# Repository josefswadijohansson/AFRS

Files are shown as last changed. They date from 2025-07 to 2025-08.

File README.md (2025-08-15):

# AFRS

[][cc-by-nc-sa]

Just a fun side electronic project, an Automatic Fishing Reel Spooler(not for when you are on the lake, but before when you are putting line on the fishing reel).

## Demostration

[Showcasing Video](https://www.youtube.com/shorts/x-qOwM7sNGY)

## Software Used

- [FreeCAD 1.0](https://www.freecad.org/)
- [OrcaSlicer](https://orcaslicer.com/)
- [Blender](https://www.blender.org/)

## Library Used
- LittleFS
- AccelStepper
- ArduinoJson
- Wifi
- Webserver

## Concept Picture
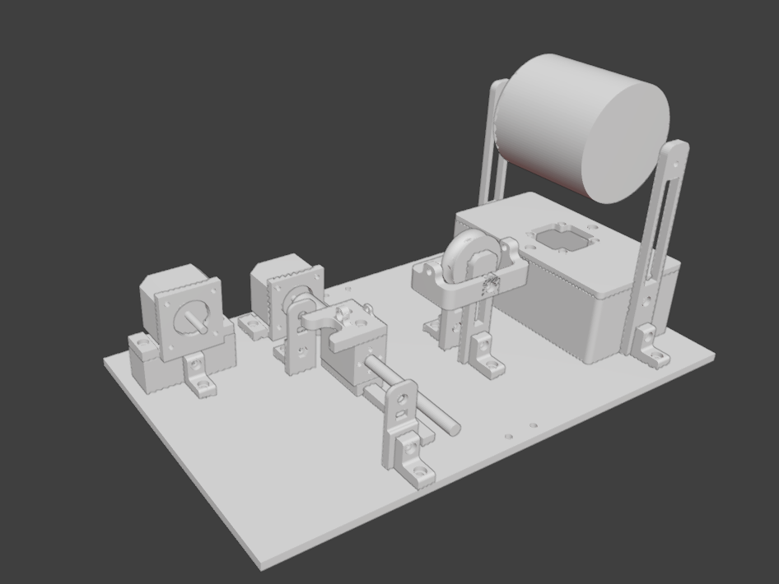
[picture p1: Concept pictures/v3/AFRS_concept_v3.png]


## End Result
<p float="left">
  
  
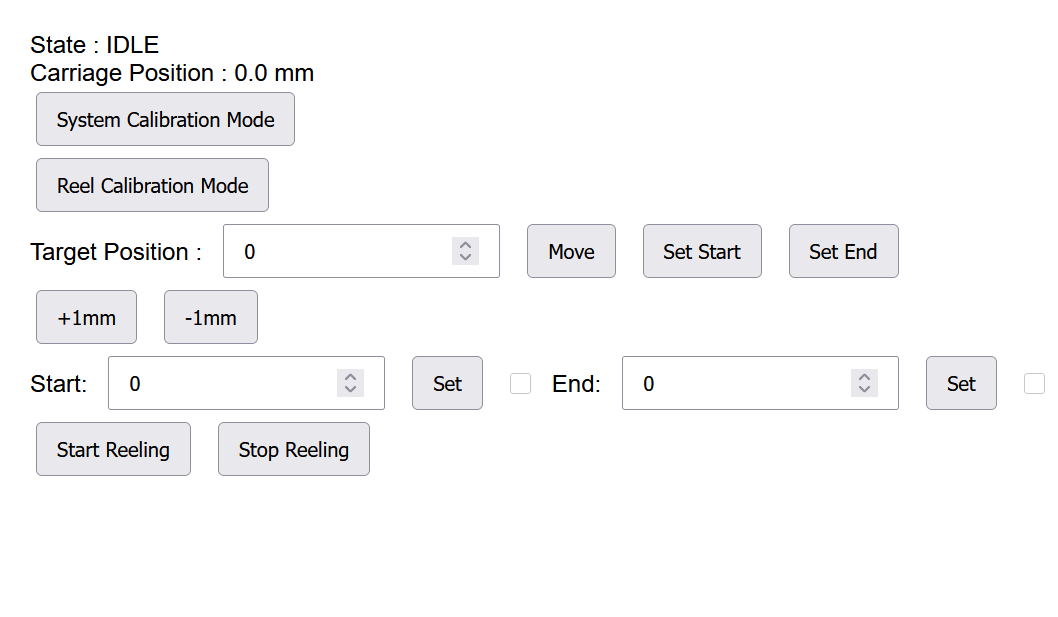
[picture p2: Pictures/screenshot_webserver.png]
  
</p>

## Components used

- 2x ESP32-C3 Mini development boards
- 2x Small "Pancake" variants of Nema 17
- 2x TMC2208 Driver module
- 150mm T8 Leadscrew
- 100mm Linear rail
- 3.3v Small laser guide
- 2x Push buttons acting as limit switches

## Improvements and fixes

- For the fishing line distance measuring, i was planning on having a measuring wheel with magnets glued to them, and when fishing line was reeled on to the new fishing reel it would spin and activate a hall sensor and for each pulse a distance would be added to the counting, issue is when i had printed the measuring wheel and then glued magnets, i realised that the hall sensor only activated on one polarity, which i didn't know. To not have this issue blocking the development of the webserver i instead removed and put that part of the project in pause for later testing and adding in later. So in the future i want the user to be able to set a X amount of meters of line to be only feed to the reel via the webserver interface.
- For now it uses TCP communication, issue is that since status update is wanted on the webserver to know the device position and state, TCP is a bit blocking on the ESP32, meaning i would prefer to maybe use UDP or some other communcation type to not block the device but to know the status of the device in the future.
- Could make the webserver interface better looking and user friendly, for now it's in the most basic form, issue i wanted to reduce file size since i had limited 400kb memory on the ESP32-C3
- Instead of hosting a webserver i could develop a desktop .NET program that talks to the ESP32-C3 devices

## License

This work is licensed under a
[Creative Commons Attribution-NonCommercial-ShareAlike 4.0 International License][cc-by-nc-sa].

[][cc-by-nc-sa]

[cc-by-nc-sa]: http://creativecommons.org/licenses/by-nc-sa/4.0/
[cc-by-nc-sa-image]: https://licensebuttons.net/l/by-nc-sa/4.0/88x31.png
[cc-by-nc-sa-shield]: https://img.shields.io/badge/License-CC%20BY--NC--SA%204.0-lightgrey.svg

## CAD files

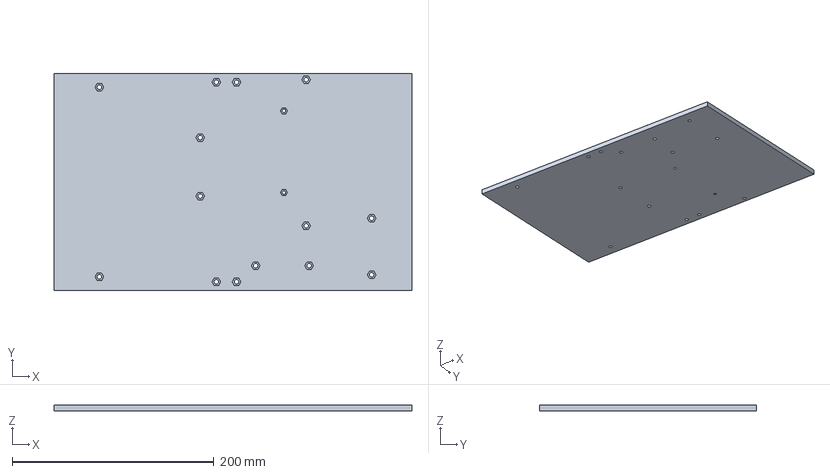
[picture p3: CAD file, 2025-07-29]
CAD/V3/BasePlate/BasePlate.FCStd
355.0 x 215.0 x 6.00 mm

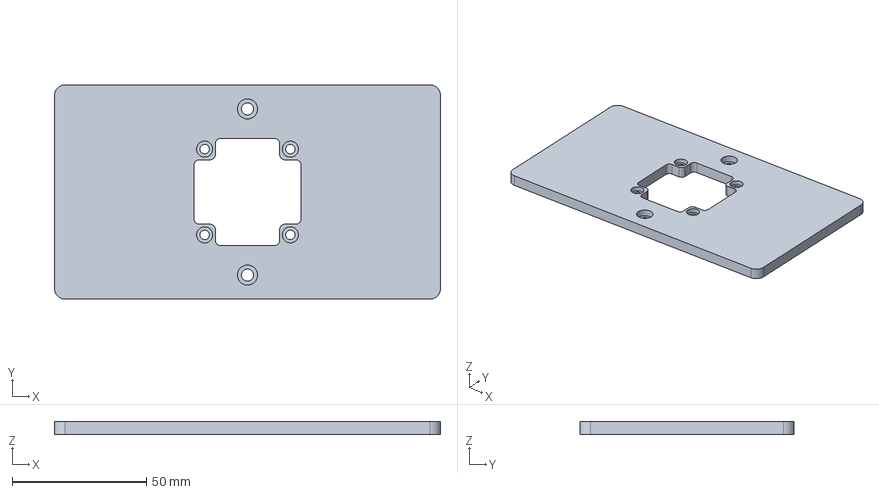
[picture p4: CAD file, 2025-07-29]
CAD/V3/ElectronicHub/ElectronicHub-Lid.FCStd
144.0 x 80.0 x 5.00 mm

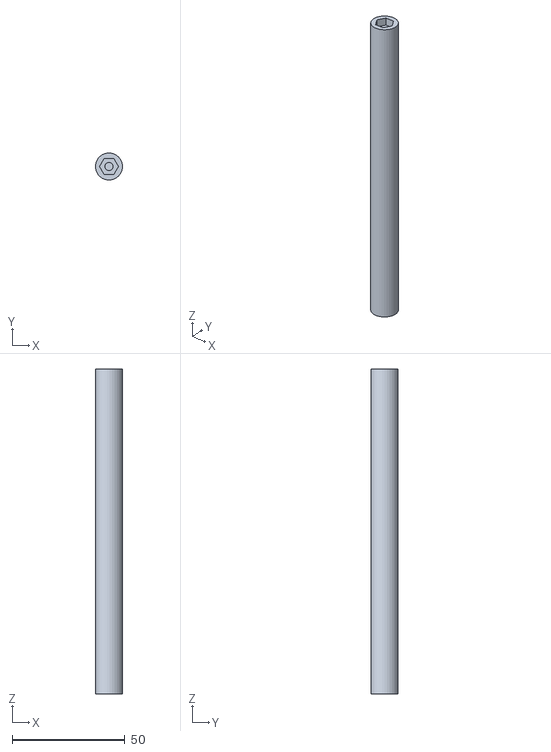
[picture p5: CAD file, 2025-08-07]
CAD/V3/FishingLineAxle/FishingLineAxle-Body.stl
12.0 x 12.0 x 144.0

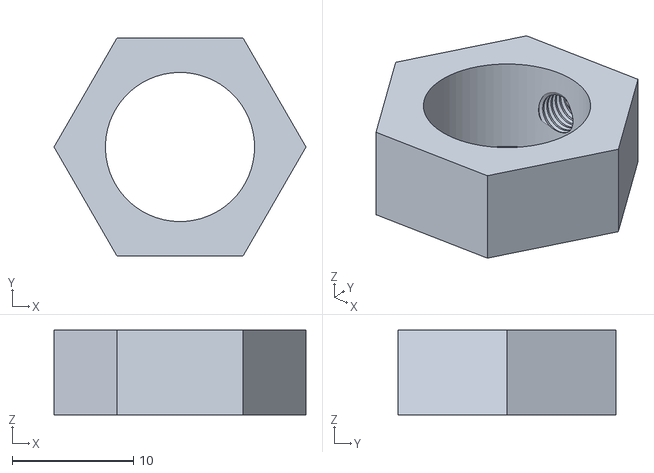
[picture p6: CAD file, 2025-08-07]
CAD/V3/FishingLineAxleTensioningNut/FishingLineAxleTensioningNut-Body.stl
20.8 x 18.0 x 7.00

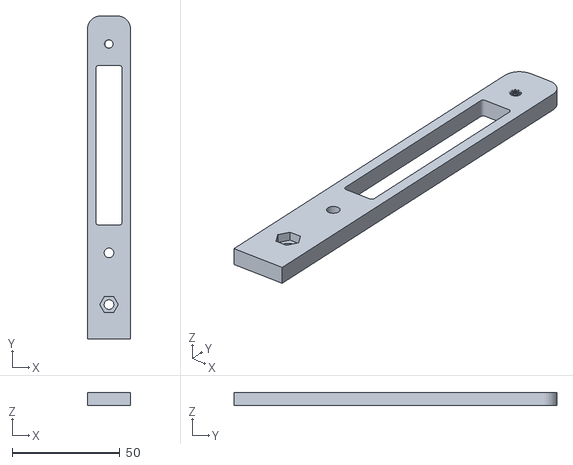
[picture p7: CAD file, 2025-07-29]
CAD/V3/FishingLineSpoolArm/FishingLineSpoolArm-Body.stl
20.0 x 150.0 x 6.00

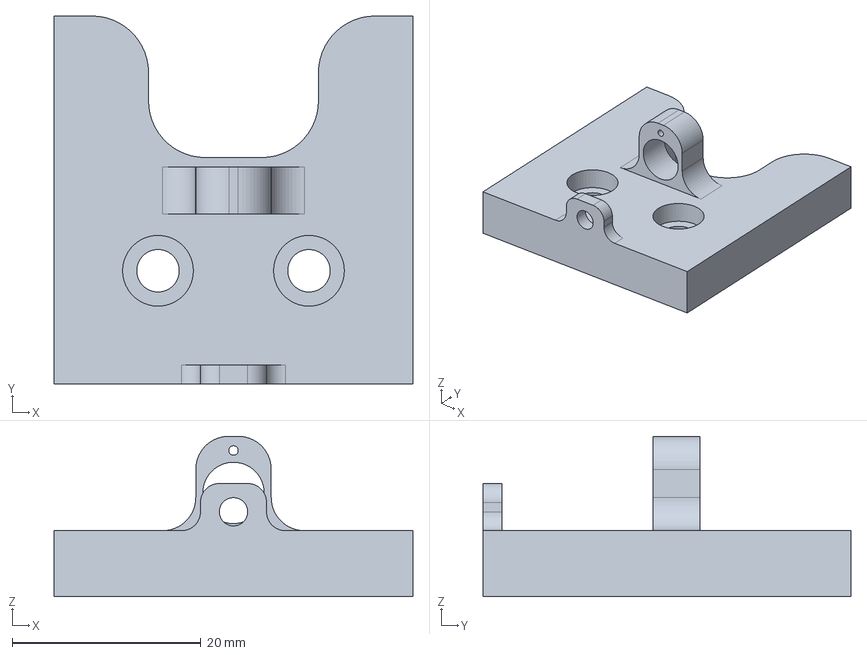
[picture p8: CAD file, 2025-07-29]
CAD/V3/Guide/Guide.FCStd
38.0 x 39.0 x 17.0 mm

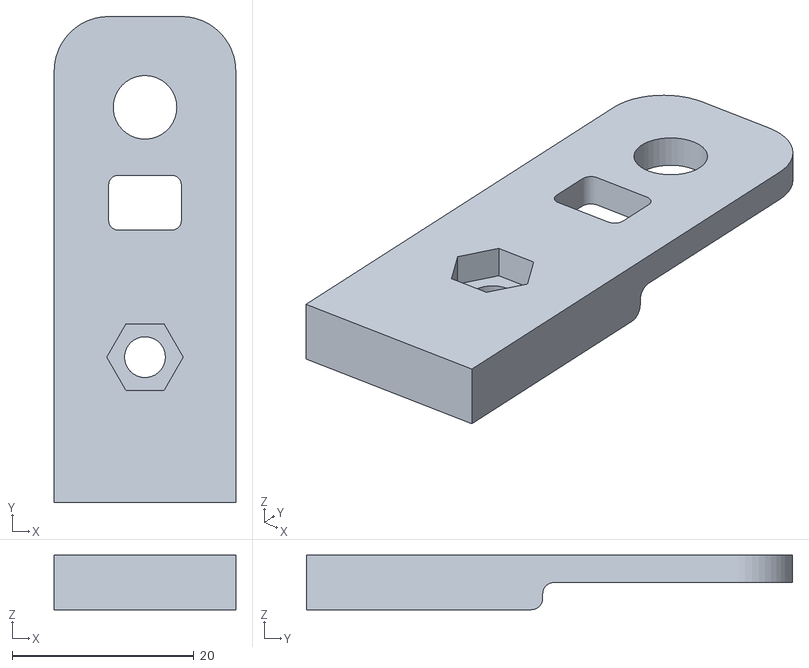
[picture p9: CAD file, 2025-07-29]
CAD/V3/LimitSwitchArm/LimitSwitchArm-Body.stl
20.0 x 53.5 x 6.00

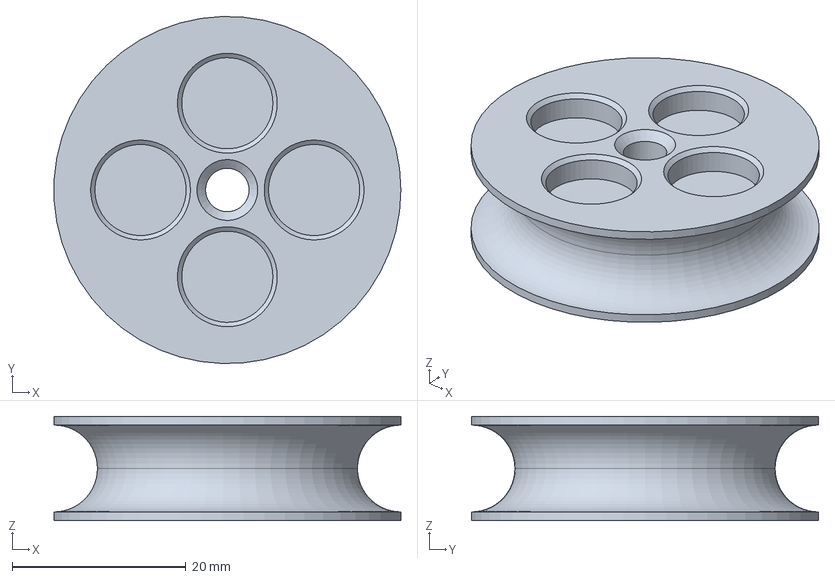
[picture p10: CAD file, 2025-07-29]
CAD/V3/MeasuringWheel/MeasuringWheel.FCStd
40.0 x 40.0 x 12.0 mm

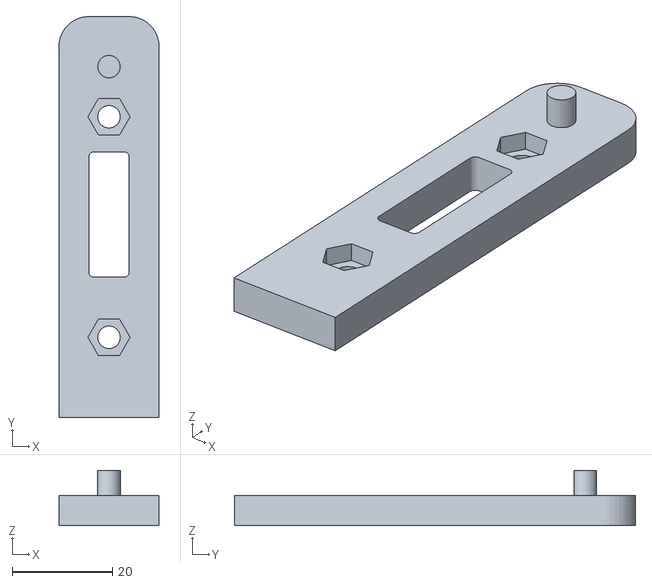
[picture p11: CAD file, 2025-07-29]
CAD/V3/MeasuringWheelArm/MeasuringWheelArm-Body.stl
20.0 x 80.0 x 11.0

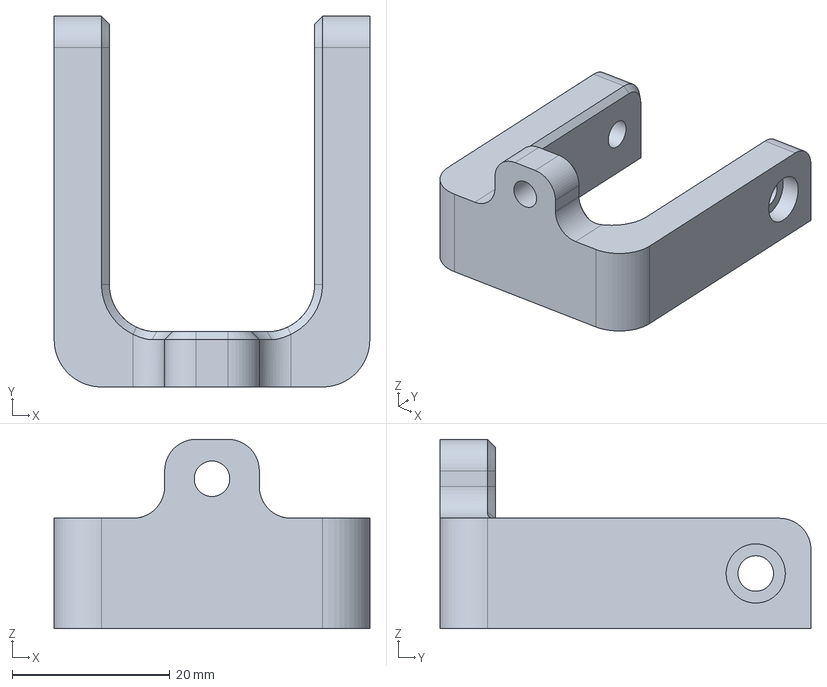
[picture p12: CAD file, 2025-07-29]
CAD/V3/MeasuringWheelArmAttachment-Guide/MeasuringWheelArmAttachment-Guide.FCStd
40.0 x 47.0 x 24.0 mm

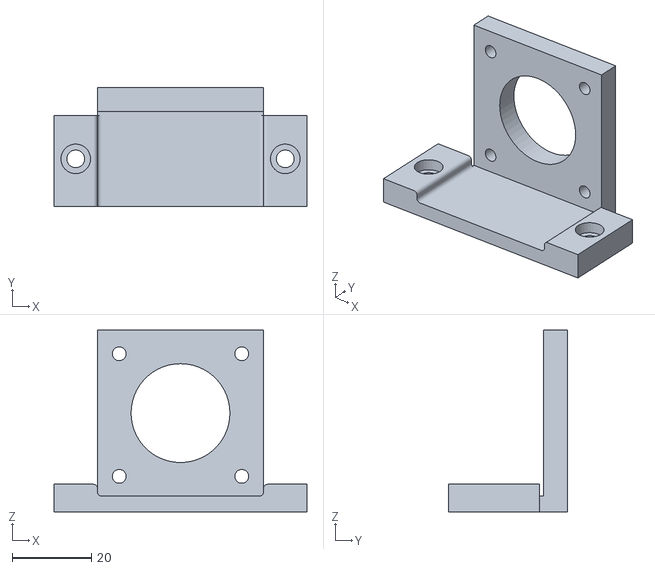
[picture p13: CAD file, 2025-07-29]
CAD/V3/Nema17Bracket/Nema17-Bracket-Body-v2.stl
64.0 x 30.0 x 46.0

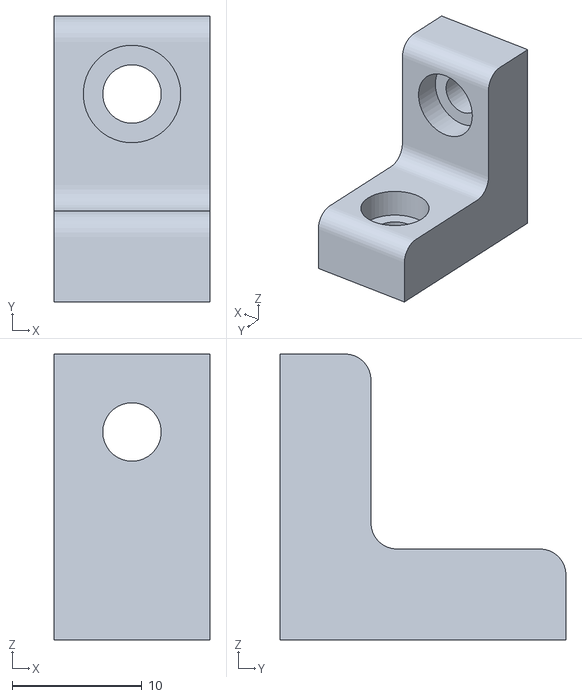
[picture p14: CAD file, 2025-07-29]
CAD/V3/PartLinker/PartLinker-Body.stl
12.0 x 22.0 x 22.0

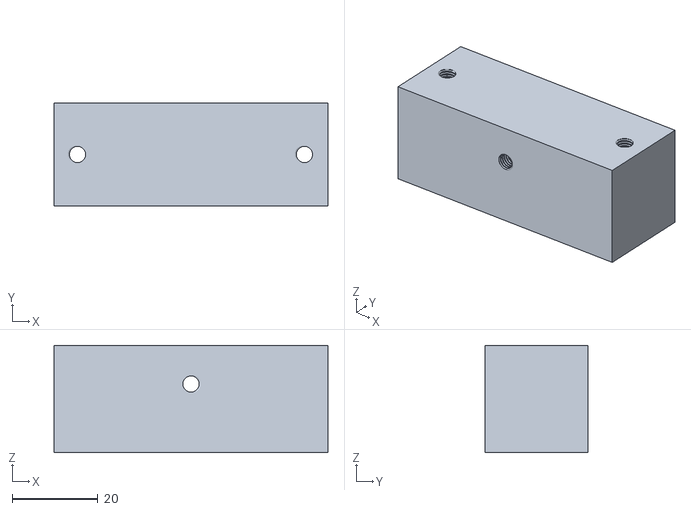
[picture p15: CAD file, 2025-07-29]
CAD/V3/ReelMotorMountAdapterBlock/ReelMotorMountAdapterBlock-Body.stl
64.0 x 24.0 x 25.0

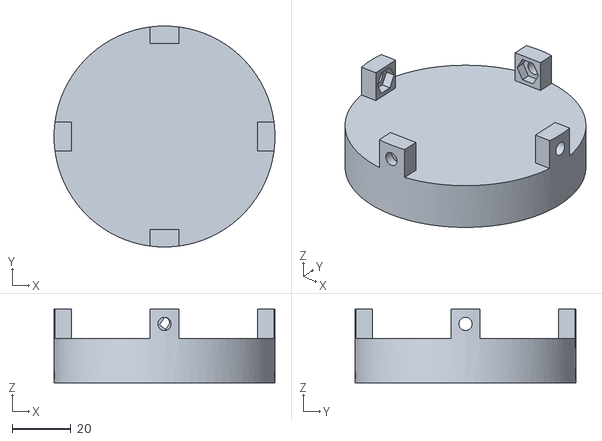
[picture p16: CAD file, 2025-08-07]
CAD/V3/ReelMount/ReelMount-Body-v3.stl
75.0 x 75.0 x 25.0

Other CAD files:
CAD/V3/BasePlate/BasePlate-Body-1.stl
CAD/V3/ElectronicHub/ElectronicHub-Body.stl
CAD/V3/FishingLineAxle/FishingLineAxle-Body-correction.stl
CAD/V3/FishingLineAxleTensioningNut/FishingLineAxleTensioningNut.FCStd
CAD/OLD_CAD_FILES/BasePlate/BasePlateAFRS-Link-Body.stl
CAD/OLD_CAD_FILES/BasePlate/BasePlateAFRS-Link.FCStd
CAD/OLD_CAD_FILES/BasePlate/BasePlateAFRS-Part1.stl
CAD/OLD_CAD_FILES/BasePlate/BasePlateAFRS-Part2.stl
CAD/OLD_CAD_FILES/BasePlate/BasePlateAFRS-v2-Body.stl
CAD/OLD_CAD_FILES/BasePlate/BasePlateAFRS-v2.FCStd
CAD/OLD_CAD_FILES/BasePlate/BasePlateAFRS.FCStd
CAD/OLD_CAD_FILES/BasePlate/BasePlateAFRS.stl
CAD/OLD_CAD_FILES/Crank-and-Slide/Carriage/Carriage-Body-v2.stl
CAD/OLD_CAD_FILES/Crank-and-Slide/Carriage/Carriage-Body.stl
CAD/OLD_CAD_FILES/Crank-and-Slide/Carriage/Carriage.FCStd
CAD/OLD_CAD_FILES/Crank-and-Slide/CarriageLineGuide/CarriageLineGuide-Body.stl
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

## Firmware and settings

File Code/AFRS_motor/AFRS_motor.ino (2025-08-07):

#include <AccelStepper.h>
#include <ArduinoJson.h>
#include <WiFi.h>

// === Pin Definitions ===
#define M1_STEP_PIN 0    // Reel motor step
#define M1_DIR_PIN  1    // Reel motor direction

#define M2_STEP_PIN 2    // Carriage motor step
#define M2_DIR_PIN  3    // Carriage motor direction

#define START_SW_PIN 6    // Home limit switch
#define END_SW_PIN  5    // End limit switch

// Wi-Fi credentials
const char* ssid = "";
const char* password = "";

WiFiServer motorServer(3333);  // Open port 3333
WiFiClient activeClient;       // Store the current client

String recvBuffer = "";

AccelStepper reelMotor(AccelStepper::DRIVER, M1_STEP_PIN, M1_DIR_PIN);
AccelStepper carriageMotor(AccelStepper::DRIVER, M2_STEP_PIN, M2_DIR_PIN);

// === Motor Configuration ===
const int MOTOR_STEPS = 200;                    // 200 steps/rev for NEMA 17
const int MICROSTEPPING = 8;                    // Set on driver board (MS1/MS2 jumpers)
const float DISTANCE_PER_REVOLUTION = 2.0;      // mm per revolution (best to do a revolution by hand and measure distance and input it here)
const float STEPS_PER_MM = (MOTOR_STEPS * MICROSTEPPING) / DISTANCE_PER_REVOLUTION;

// === Speed Settings ===
const float REEL_RPM = 40;    // Reel motor speed
float CARRIAGE_RPM = 100;     // Carriage motor speed (will be dynamically set)
#define FORWARD -1            // In my setup the carriage is moving forward is in negative speed, meaning away from the motor, that why we need to invert the movement in tracking

// System state management
enum SystemState {
  IDLE,
  SYSTEM_CALIBRATION,
  REEL_CALIBRATION,
  REELING
};
SystemState currentSystemState = IDLE;

enum SystemCalibrationState {
  FIND_START,
  FIND_END
};
SystemCalibrationState systemCalibrationState = FIND_START;

// Position tracking
float railLength = 0;
float currentPositionMM = 0;
float targetPosition = 0;
bool isMovingToEnd = false;

// Gap values
float reelGapStartPosition = -1;
float reelGapEndPosition = -1;

bool starterSet = false;  // Is start gap position set?
bool endSet = false;      // Is start gap position set?

void setup() {
  Serial.begin(115200);

  Serial.println("Motor ESP Connecting");
  // Connect to Wi-Fi
  WiFi.begin(ssid, password);
  while (WiFi.status() != WL_CONNECTED) {
    delay(500);
    Serial.print(".");
  }
  Serial.println("\nMotor ESP connected. IP: " + WiFi.localIP().toString());

  // FIXME : Perhaps use UDP communication instead maybe it will not block the ESP32C3 as much
  motorServer.begin();  // Start TCP server

  pinMode(START_SW_PIN, INPUT_PULLUP);
  pinMode(END_SW_PIN, INPUT_PULLUP);

  // Configure reel motor
  reelMotor.setMaxSpeed((REEL_RPM * MOTOR_STEPS * MICROSTEPPING) / 60.0);
  reelMotor.setSpeed(-reelMotor.maxSpeed());  // To reel the line in toward the fishing reel, i need the fishing reel to move anti-clockwise
  reelMotor.setMinPulseWidth(50);

  // Configure carriage motor
  carriageMotor.setMaxSpeed((CARRIAGE_RPM * MOTOR_STEPS * MICROSTEPPING) / 60.0);
  carriageMotor.setSpeed(carriageMotor.maxSpeed());
  carriageMotor.setMinPulseWidth(50);
}

void loop() {
  // Accept new clients
  if (!activeClient || !activeClient.connected()) {
    activeClient = motorServer.available();
  }

  if (activeClient && activeClient.connected() && activeClient.available()) {
    while (activeClient.available()) {
      char c = activeClient.read();

      if (c == '\n') {
        recvBuffer.trim();  // Remove trailing \r or whitespace
        if (recvBuffer.length() > 0) {
          handleCommand(recvBuffer, activeClient);
        }
        recvBuffer = "";  // Reset for next command
      } else {
        recvBuffer += c;
        // Optional: protect against overflow
        if (recvBuffer.length() > 200) recvBuffer = "";  // Reset if too long
      }
    }
  }

  // Main state machine
  switch (currentSystemState) {
    case IDLE: break;
    case REELING: runReeling(); break;
    case REEL_CALIBRATION: runCalibration(); break;
    case SYSTEM_CALIBRATION:
      if (systemCalibrationState == FIND_START) runFindStart();
      else if (systemCalibrationState == FIND_END) runFindEnd();
      break;
  }
}

void runFindStart() {
  // Force the carriage motor to find the start switch by moving it positive direction, meaning toward the motor
  if(carriageMotor.speed() <= 0){ 
    carriageMotor.setSpeed(carriageMotor.maxSpeed());
  }

  carriageMotor.runSpeed();

  // 
  if (digitalRead(START_SW_PIN) == LOW) {
    carriageMotor.stop();
    carriageMotor.setSpeed(0);
    currentPositionMM = 0;  // Start from zero
    carriageMotor.setCurrentPosition(0);
    carriageMotor.setSpeed(carriageMotor.maxSpeed());  // Always move forward from here
    systemCalibrationState = FIND_END;
  }
}

void runFindEnd() {

  // Force the carriage motor to find the end switch by moving it negative direction, meaning away from the motor
  if(carriageMotor.speed() >= 0){
    carriageMotor.setSpeed(carriageMotor.maxSpeed() * FORWARD);
  }

  if (carriageMotor.runSpeed()) {
    currentPositionMM += (1.0 / STEPS_PER_MM); // Calculate the new position when the motor actually does steps
  }

  if (digitalRead(END_SW_PIN) == LOW) {
    carriageMotor.stop();
    carriageMotor.setSpeed(0);

    railLength = currentPositionMM; // Assign the maximum length the motor can travel
    targetPosition = railLength;

    currentSystemState = IDLE;
  }
}

void runReeling() {
  
  if(reelGapStartPosition < 0 || reelGapEndPosition < 0){
    // TODO : Maybe throw an error for the user
    stopMotors();
    return;
  }

  if (isWithinRange(currentPositionMM, reelGapStartPosition, reelGapEndPosition)) {

    if(reelMotor.speed() == 0){
      reelMotor.setSpeed(-reelMotor.maxSpeed());
    }
    reelMotor.runSpeed();
  }

  // === Oscillate effect === 
  if (!isMovingToEnd) {
    if (runMoveToPosition(reelGapStartPosition)) {
      isMovingToEnd = true;
    }
  } else {
    if (runMoveToPosition(reelGapEndPosition)) {
      isMovingToEnd = false;
    }
  }
}

void runCalibration() {
  runMoveToPosition(targetPosition);
}

bool runMoveToPosition(float position) {

  // If it want's to move out of bounds, stop the motors, maybe it will damage the setup
  if(position < 0.0f || position > railLength){
    stopMotors();
    return false;
  }

  float distance = abs(currentPositionMM - position);
  float margin = 0.01f;

  if (distance <= margin) {
    carriageMotor.setSpeed(0);
    carriageMotor.stop();
    return true;
  }

  int direction = sign(position - currentPositionMM);
  int previousDirection = (carriageMotor.speed() / FORWARD) / carriageMotor.maxSpeed();

  if (previousDirection != direction) {
    carriageMotor.setSpeed(carriageMotor.maxSpeed() * direction * FORWARD);
  }

  if (carriageMotor.runSpeed()) {
    currentPositionMM += (carriageMotor.speed() > 0) ? (-1.0 / STEPS_PER_MM) : (1.0 / STEPS_PER_MM);

    if (distance <= margin) {
      carriageMotor.setSpeed(0);
      carriageMotor.stop();
      return true;
    }
  }

  return false;
}

void stopMotors(){
    currentSystemState = IDLE;
    carriageMotor.stop();
    carriageMotor.setSpeed(0);
    reelMotor.stop();
    reelMotor.setSpeed(0);
}

float calculateCarriageRPM(float reelRPM, float gapLengthMM) {
  float timeForReelRevs = 4.0f * 60.0f / reelRPM;
  float mmPerSec = gapLengthMM / timeForReelRevs;
  float carriageRevsPerSec = mmPerSec / DISTANCE_PER_REVOLUTION;
  return carriageRevsPerSec * 60.0f;
}

bool isWithinRange(float currentPosition, float start, float end) {
  return currentPosition >= start && currentPosition <= end;
}

float sign(float value) {
  return float((value > 0) - (value < 0));
}

String stateToString(SystemState systemState) {
  switch(systemState) {
    case IDLE: return "IDLE";
    case REELING: return "REELING";
    case REEL_CALIBRATION: return "REEL_CALIBRATION";
    case SYSTEM_CALIBRATION: return "SYSTEM_CALIBRATION";
    default: return "UNKNOWN";
  }
}

void handleCommand(const String& cmd, WiFiClient& client) {
  if (cmd.startsWith("starter-position-input")) {
    float value;
    int scanned = sscanf(cmd.c_str(), "starter-position-input %f", &value);
    if (scanned == 1) {
      reelGapStartPosition = value;
      starterSet = true;

      if (starterSet && endSet) {
        float gap = reelGapEndPosition - reelGapStartPosition;
        float newCarriageRPM = calculateCarriageRPM(REEL_RPM, gap);
        CARRIAGE_RPM = newCarriageRPM;
        float maxSpeed = (newCarriageRPM * MOTOR_STEPS * MICROSTEPPING) / 60.0;
        carriageMotor.setMaxSpeed(maxSpeed);
      }

      client.println("OK");
    } else {
      client.println("Invalid starter-position-input command");
    }

  } else if (cmd.startsWith("end-position-input")) {
    float value;
    int scanned = sscanf(cmd.c_str(), "end-position-input %f", &value);
    if (scanned == 1) {
      reelGapEndPosition = value;
      endSet = true;

      if (starterSet && endSet) {
        float gap = reelGapEndPosition - reelGapStartPosition;
        float newCarriageRPM = calculateCarriageRPM(REEL_RPM, gap);
        CARRIAGE_RPM = newCarriageRPM;
        float maxSpeed = (newCarriageRPM * MOTOR_STEPS * MICROSTEPPING) / 60.0;
        carriageMotor.setMaxSpeed(maxSpeed);
      }

      client.println("OK");
    } else {
      client.println("Invalid end-position-input command");
    }
  } else if (cmd == "status") {
    StaticJsonDocument<200> doc;
    doc["position"] = currentPositionMM;
    doc["state"] = stateToString(currentSystemState);
    doc["railLength"] = railLength;
    doc["starterSet"] = starterSet;
    doc["endSet"] = endSet;
    String json;
    serializeJson(doc, json);
    client.println(json);

  } else if (cmd == "calibrate") {
    currentSystemState = SYSTEM_CALIBRATION;
    systemCalibrationState = FIND_START;
    client.println("System calibration started");

  } else if (cmd == "reel_cal") {
    if(currentSystemState != REEL_CALIBRATION){
      currentSystemState = REEL_CALIBRATION;
      
    } else {
      currentSystemState = IDLE;
    }

    if(starterSet && endSet){
      targetPosition = (reelGapEndPosition - reelGapStartPosition) / 2.0f;
    }else {
      targetPosition = 0;
    }

    client.println("Reel calibration mode");

  } else if (cmd == "start") {
    if (starterSet && endSet) {
      currentSystemState = REELING;
      client.println("Started reeling");
    } else {
      client.println("Error: Gap not set");
    }

  } else if (cmd == "stop") {
    stopMotors();
    client.println("Stopped");
  } else if (cmd.startsWith("move")) {
    float value;
    int scanned = sscanf(cmd.c_str(), "move %f", &value);
    if (scanned == 1) {
      targetPosition = value;
      currentSystemState = REEL_CALIBRATION;  // Use existing logic to move to target
      client.println("OK");
    } else {
      client.println("Invalid end-position-input command");
    }

  }else {
    client.println("Unknown command");
  }
}

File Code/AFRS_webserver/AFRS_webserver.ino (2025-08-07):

#include <WiFi.h>
#include <WebServer.h>
#include <ArduinoJson.h>
#include <LittleFS.h>

// Wi-Fi credentials
const char* ssid = "";
const char* password = "";

// Web server on port 80
WebServer server(80);

// TCP client for talking to motor ESP
WiFiClient motorClient;
IPAddress motorIP(192, 168, 1, 18); // Motor ESP IP (must be static or fixed by DHCP)

bool starterSet = false;
bool endSet = false;

// =================== COMMUNICATION ===================

bool ensureConnected() {
  if (!motorClient.connected()) {
    return motorClient.connect(motorIP, 3333);  // Port must match motor ESP
  }
  return true;
}

String sendMotorCommand(const String& cmd) {
  if (!ensureConnected()) return "Motor Not Connected";

  motorClient.println(cmd);
  motorClient.flush();

  String response = "";
  unsigned long start = millis();
  while (millis() - start < 300) {
    while (motorClient.available()) {
      char c = motorClient.read();
      if (c == '\n') return response;
      response += c;
    }
  }
  return response;
}

// =================== SETUP ===================

void setup() {
  Serial.begin(115200);

  // Connect to Wi-Fi
  WiFi.begin(ssid, password);
  while (WiFi.status() != WL_CONNECTED) {
    delay(500);
    Serial.print(".");
  }
  Serial.println("\nConnected to Wi-Fi. IP: " + WiFi.localIP().toString());

  if (!LittleFS.begin(true)) {
    Serial.println("Failed to mount LittleFS");
    return;
  }

  // Routes
  server.on("/", handleRoot);
  server.on("/cmd", handleCommand);
  server.on("/move", handleMove);
  server.on("/set", handleSet);
  server.on("/status", handleStatus);

  server.begin();
}

void loop() {
  server.handleClient();
}

// =================== WEB HANDLERS ===================

void handleRoot() {
  File file = LittleFS.open("/index.html", "r");
  if (!file) {
    server.send(500, "text/plain", "Failed to load HTML file");
    return;
  }
  server.streamFile(file, "text/html");
  file.close();
}

void handleCommand() {
  String command = server.arg("code");

  String reply = sendMotorCommand(command);
  server.send(200, "text/plain", reply.length() > 0 ? reply : "OK");
}

void handleSet() {
  if (!server.hasArg("type") || !server.hasArg("val")) {
    server.send(400, "text/plain", "Missing arguments");
    return;
  }

  String type = server.arg("type");
  float value = server.arg("val").toFloat();

  if (type == "starter-position-input") {
    starterSet = true;
    String cmd = "starter-position-input " + String(value, 2);
    sendMotorCommand(cmd);
  } else if (type == "end-position-input") {
    endSet = true;
    String cmd = "end-position-input " + String(value, 2);
    sendMotorCommand(cmd);
  } else {
    server.send(400, "text/plain", "Invalid type");
    return;
  }

  server.send(200, "text/plain", "OK");
}

void handleStatus() {
  String json = sendMotorCommand("status");
  if (json.startsWith("{")) {
    server.send(200, "application/json", json);
  } else {
    server.send(500, "text/plain", "Invalid status");
  }
}

void handleMove() {
  float position = server.arg("pos").toFloat();
  String cmd = "move " + String(position, 2);
  sendMotorCommand(cmd);

  // MUST send a response to complete the request
  server.send(200, "text/plain", "OK");
}

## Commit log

2025-05-24 added CAD files and concept pictures to the repo
    [BasePlateAFRS-Link-Body.stl, BasePlateAFRS-Link.FCStd, BasePlateAFRS-Part1.stl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]
2025-07-29 Update to CAD files, added more concept pictures, started off on the code for the electronics
    Skipped organizing and uploading v2 of the design since it was lacklusting, feel like the v3 is closer to what i will leave the project as.
    [ArmPath-Body.stl, ArmPath.FCStd, BasePlate-Body-1.stl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]
2025-08-07 Started on the webserver sketch, connected it to the motor code with tcp communication, implemented a simple webserver interface to control the device
    [FishingLineAxle-Body-correction.stl, FishingLineAxle-Body.stl, FishingLineAxleTensioningNut-Body.stl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]

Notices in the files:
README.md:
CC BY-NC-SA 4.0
